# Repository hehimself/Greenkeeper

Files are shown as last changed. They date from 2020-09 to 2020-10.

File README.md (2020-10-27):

# Greenkeeper





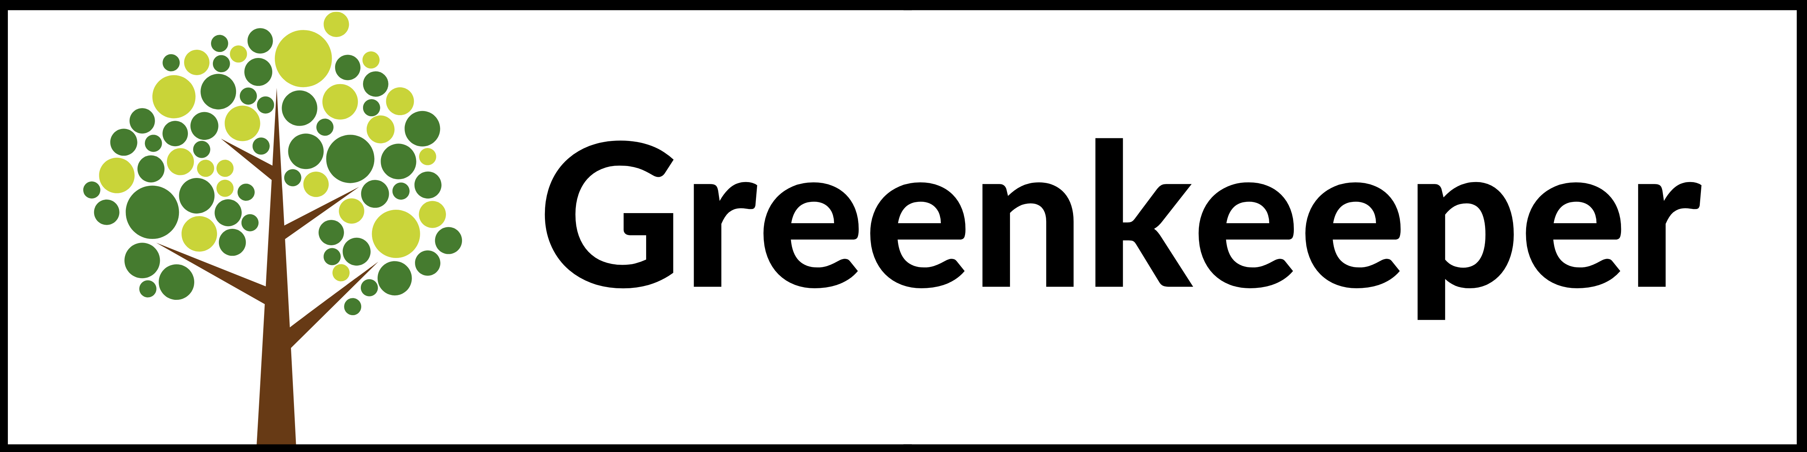
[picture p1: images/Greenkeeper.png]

Der Arduino Greenkeeper ist ein vollautomatisiertes Bewässerungssystem für eine Zimmerpflanze.
Zu Beginn habe ich eine Platine mithilfe von KiCAD erstellt. Auf der Platine können alle wichtigen Teile direkt verlötet werden. Die SMD LEDs helfen, den Status des Bewässerungssystems zu erkennen. Auf dem OLED Display werden die Messwerte wie Bodenfeuchtigkeit, Temperatur, Lichtstärke usw dargestellt. Zudem gibt es ein Menü, welches sich durch die Buttons steuern lässt.
(Schaltplan unter: schema.pdf)

## Funktionsweise
### 1. Die Bewässerung
Die Bewässerungsanlage ist recht simple aufgebaut. Es wird mithilfe des Sensor die Bodenfeuchtigkeit gemessen. Wenn der Messwert einen gewissen Wert überschreitet wird die Pumpe mithilfe des Relais für eine Sekunde aktiviert. Alle 10 Sekunden wird die Bodenfeuchtigkeit gemessen. Somit wird sichergestellt, das die Pflanze immer genügend Wasser zur Verfügung hat.

```C++
void Bewaesserungssystem() {
  //Als erstes wird eine Bodenmessung durchgeführt
  Bodenmessung();
//Falls der Boden zu trocken ist wird die Pumpe eingeschalten
  if (Bodensensor_Messwert >= 450) {        //Dieser Wert ist natürlich abhängig von Pflanze und Sensor
    if (Pumpe_Auto == 1) {
      LED_D12_Status = 1;
      LED_Steuerung();
      digitalWrite(Pumpe, LOW);
      Pumpe_counter ++;
      delay(1000);
      digitalWrite(Pumpe, HIGH);
      LED_D12_Status = 0;
    } else {
      LED_D11_Status = 1;
    }  
  } else {
    LED_D11_Status = 1;
  }
}
```

### 2. Die Status LEDs
Die Status LEDs die am meisten angeschalten sind werden, je nach Helligkeit automatisch gedimmt. Diese sind am Arduino an den PWM (Pulse Width Modulation) fähigen Pins angeschlossen.

POWER Diese LED zeigt, ob die Platine mit Strom versorgt wird
STATUS (gelb) Diese blinkt wenn etwas mit der Bewässerung nicht stimmt
STATUS (grün) Diese LED leuchtet wenn die Pflanze genügend Wasser hat
PUMPE Diese LED leuchtet wenn die Pumpe läuft
W-Tank Diese LED leuchtet, wenn der Wassertank leer ist.
FEHLER (noch ohne funktion)

### 3. Die Tasten
Taster von links nach rechts:

Menü Button
"Down" Button
"UP" Button
"ENTER" Button

### 4. Das Display
Auf dem Dashboard wird der Messwert der Bodenmessung, die Temperatur und der Messwert des Lichtsensor dargestellt. Wenn man zum Menü kommen will muss man nur den "Menü" Button betätigen (1. Button von links). Um wieder zurück zum Dashboard zu kommen wählt man im Menü den Punk "Dashboard" aus.

Das Menü hat folgende weitere Funktionen:

PUMP Automatik Hierbei lässt sich die Bewässerung ausschalten um sicher zu gehen das die Pumpe nicht läuft, obwohl der Sensor beispielsweise aus der Pflanze genommen wurde.
Nachtmodus Der Nachtmodus lässt sich über das Menü aktivieren/deaktivieren. Während der Nachtmodus aktiviert ist gehen alle Status LEDs aus.
Display Mit diesem Menü Punkt lässt sich das Display ausschalten, sodass alles Dunkel ist. Wenn man das Display wieder anschalten möchte muss man einfach den "Menü" Button (Button_S1) drücken.
Transistor Mithilfe dieser Funktion, lassen sich die Grünen LEDs unten manuell anschalten. Diese sind jedoch zurzeit nur für ein schönes aussehen und noch komplett ohne eine sinnvolle Funktion

## Die Platine
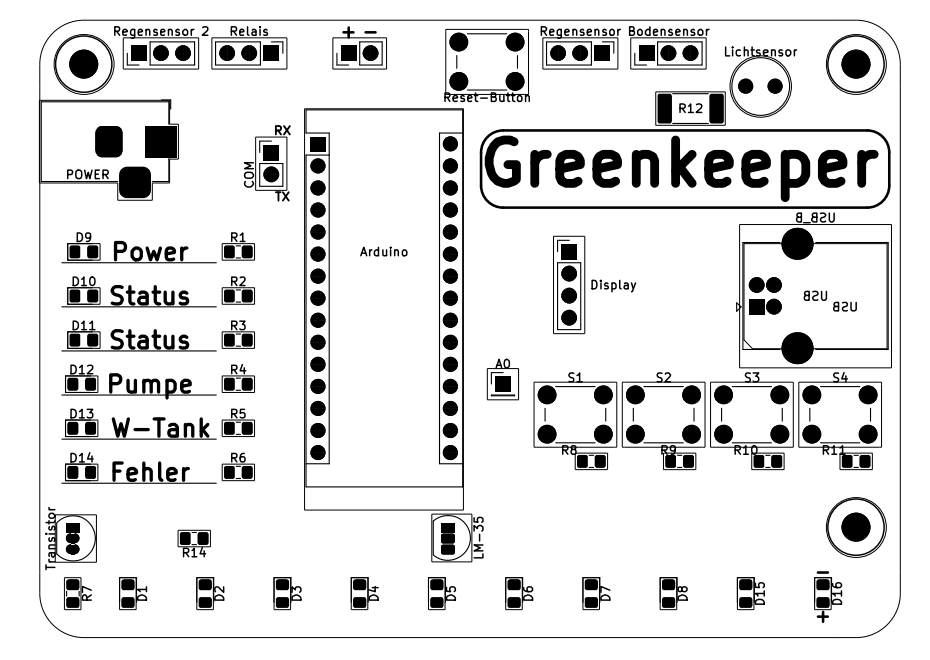
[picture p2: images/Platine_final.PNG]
Platine


## Übersicht zu Widerständen und Leds
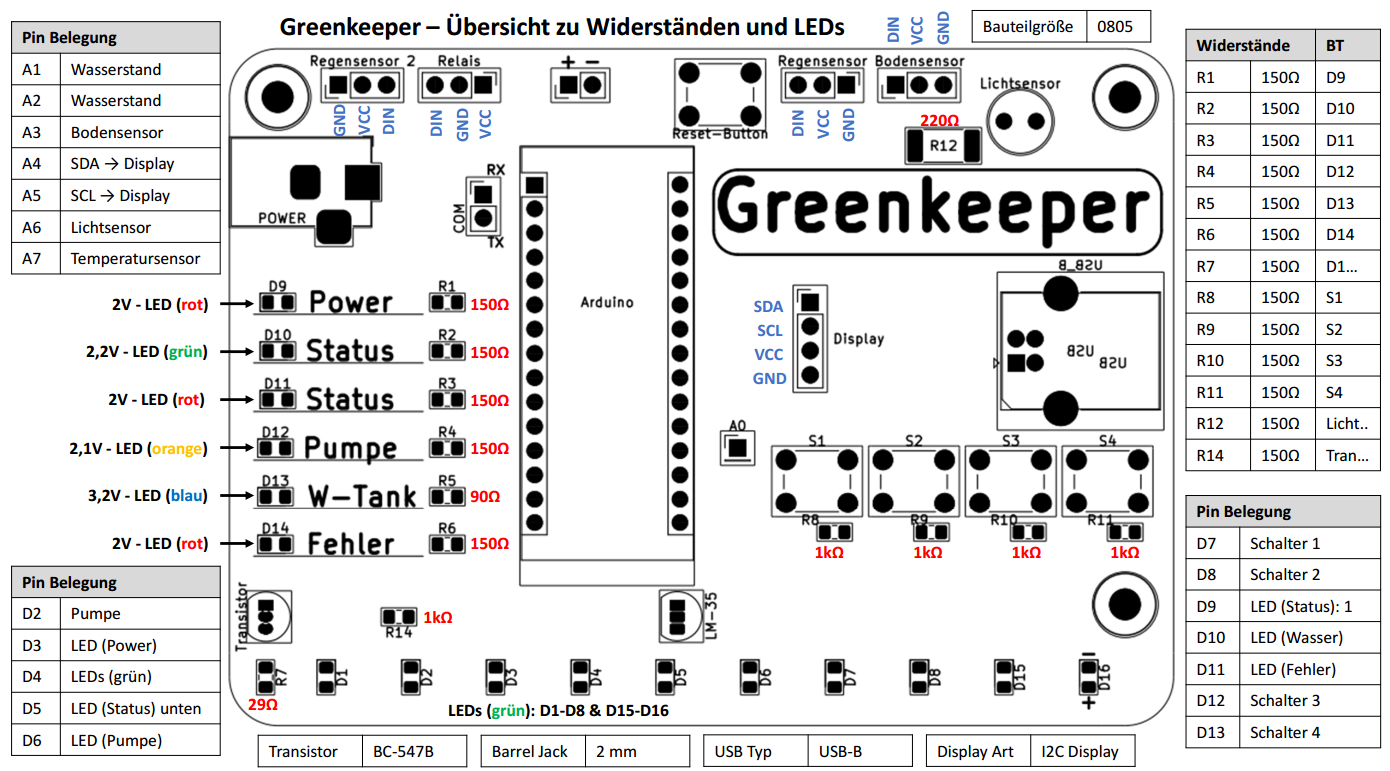
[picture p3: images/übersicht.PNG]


# Bauanleitung
Die Gesamte Anleitung gibts hier: [hackster.io](https://www.hackster.io/ms2002maerz14/arduino-greenkeeper-687363)
WARNUNG: Man sollte bereits Erfahrung im löten von SMD Komponenten der Größe 0805 besitzen, da sonst die Komponenten oder die Platine beschädigt werden können.

### Platine löten

Ich rate aus eigener Erfahrung mehrere Platinen und mehr Komponenten als angegeben sich zu kaufen, da es sehr schnell gehen kann eine SMD Komponente zu zerstören. Am Besten nimmt man sich die Übersicht zu Widerständen uns LEDs zur Hilfe während des löten, um zu wissen, welches Bauteil, wo gelötet werden muss.

### Platine testen

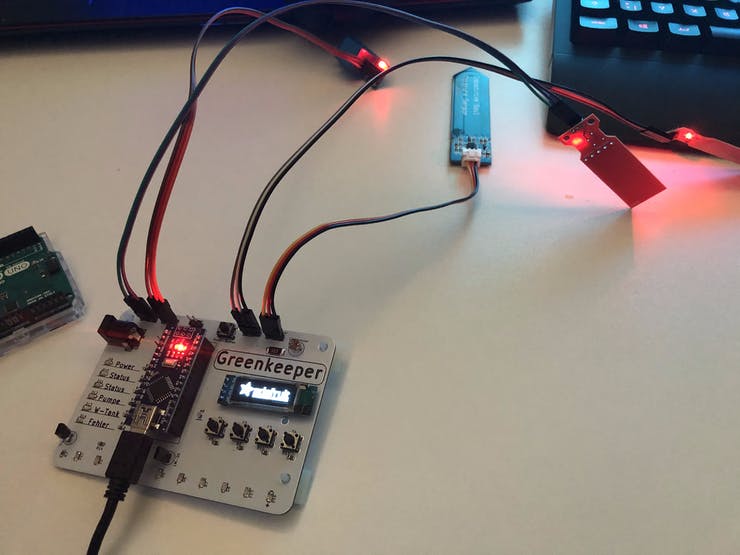
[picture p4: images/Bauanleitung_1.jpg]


Zum testen aller Funktionen und zum Einstellen der Parameter der Sensoren habe ich die Platine per USB mit dem Computer verbunden und nacheinander alle Sensoren, Schalter und Display getestet.

### Inbetriebnahme

Am Besten befestigt man den Schlauch mit ein bisschen Tesafilm an dem Topf, damit dieser während der Bewässerung nicht verrutscht. Zudem ist es nun Zeit den Sensor für die Bodenfeuchtigkeit in die Erde zu stecken.

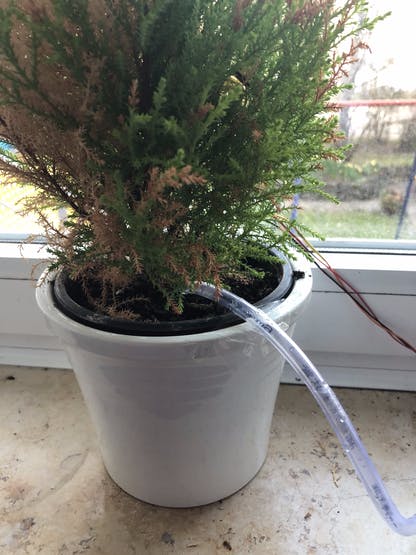
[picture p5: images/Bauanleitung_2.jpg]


Nun ist es Zeit sich um den Wassertank zu kümmer. Hierbei empfehle ich die Pumpe am Boden des Behälters oder des Tanks festzukleben. Das Relais habe ich in meinem Fall einfach an die Seite des Wasserbehälter geklebt (siehe Abbildung unten)

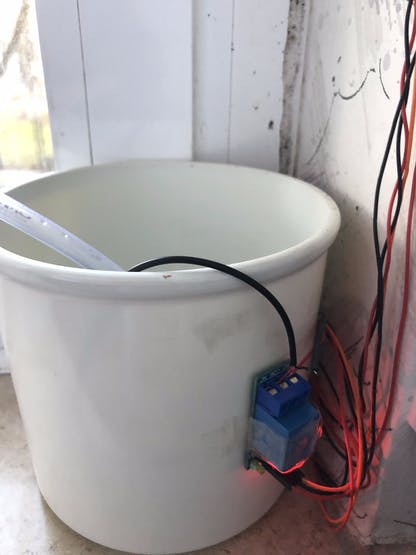
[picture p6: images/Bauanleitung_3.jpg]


Die Platine habe ich mithilfe von Platinen Abstandshalter an der Wand befestigt und im Anschluss alle Anschlüsse verkabelt. Die Stromversorgung erfolgt über ein Netzteil (9V). Eine Versorgung über USB ist zwar möglich jedoch wenn alle LEDs angeschalten sind und die Pumpe läuft, ist man an der Spitze der Leistung des Arduino. Das Bewässerungssystem ist nun einsatzbereit. Eventuell muss man im Code den Wert, ab wann die Pumpe pumpt noch für seine Pflanze anpassen.

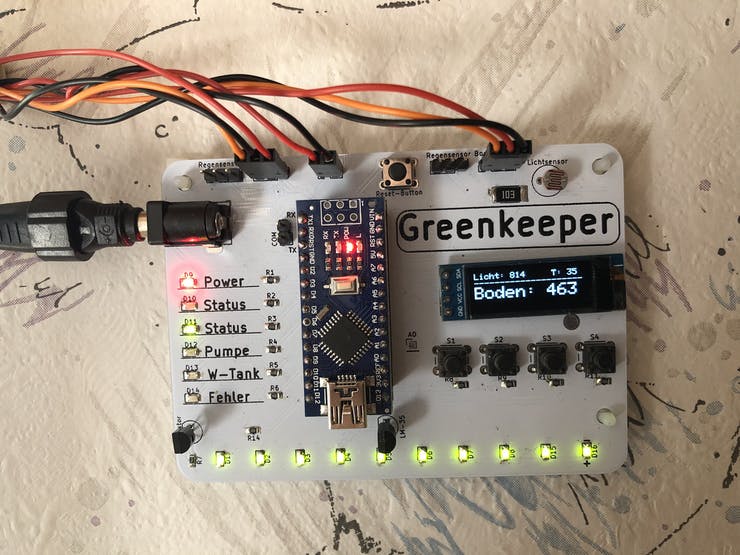
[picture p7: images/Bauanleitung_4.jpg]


Fertig...

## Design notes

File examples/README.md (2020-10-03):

## Code Beispiele
Diese Code Beispiele dienen zum testen der einzelnen Komponenten

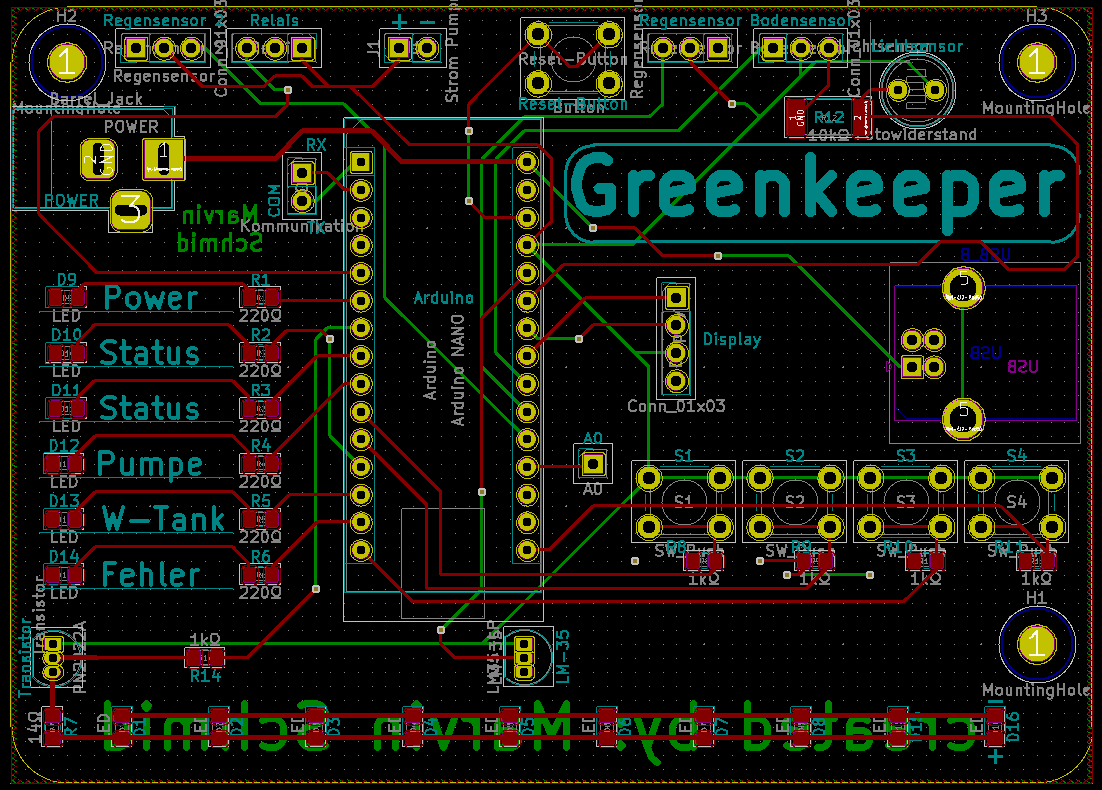
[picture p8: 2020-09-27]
images/Platine final.PNG

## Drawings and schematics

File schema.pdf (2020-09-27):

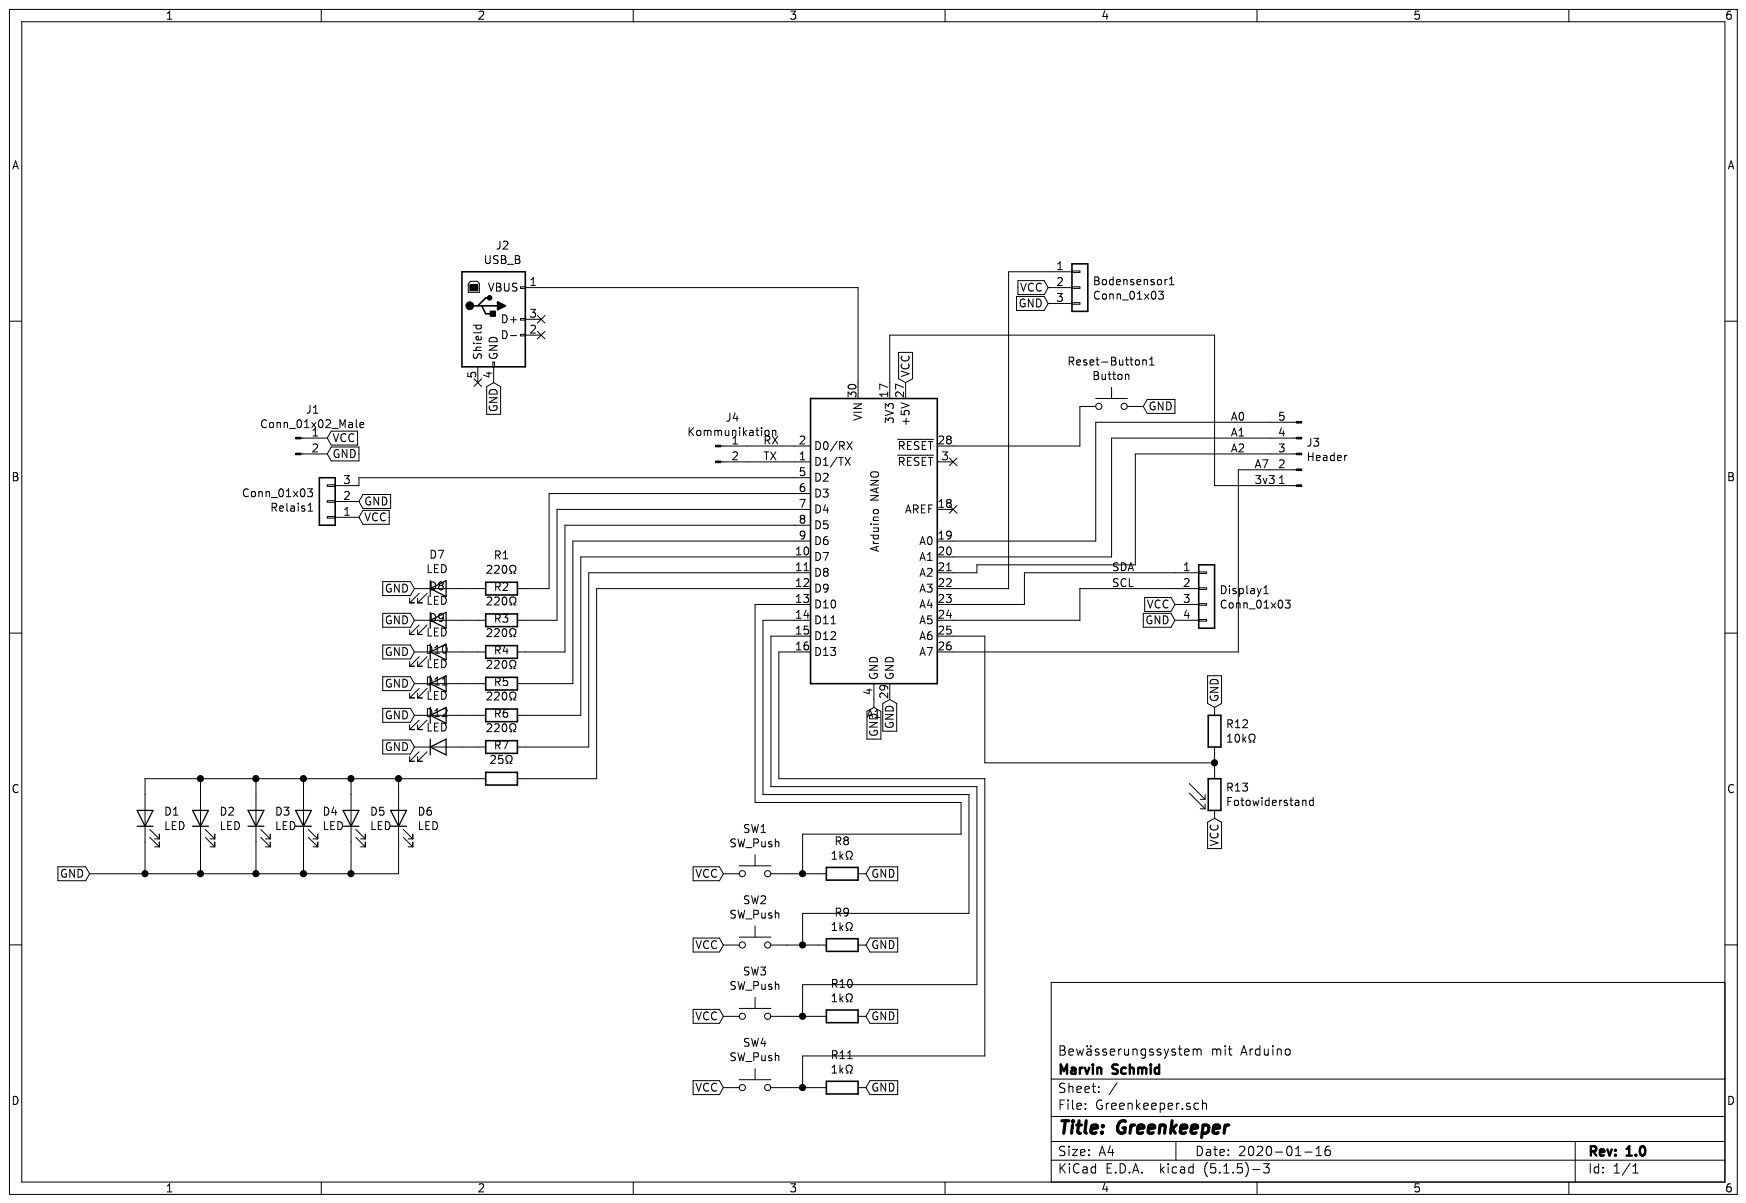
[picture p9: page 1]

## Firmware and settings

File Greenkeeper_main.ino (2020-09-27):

/* ---------------------------------------------------------*
 *                                                          *
 *    Projekt: Arduino Greenkeeper - Bewässerungssystem     *
 *                                                          *
 *    Name: Marvin Schmid                                   *
 *                                                          *
 *    Version: 1.5                                          *
 *                                                          *
 * ---------------------------------------------------------*
*/
//Bibliotheken
#include <SPI.h>
#include <Wire.h>
//Bibliotheken für den betrieb des Displays
#include <Adafruit_GFX.h>
#include <Adafruit_SSD1306.h>
 
#define OLED_RESET 4
Adafruit_SSD1306 display(OLED_RESET);

//Arduino LEDs
const int LED_D9 = 3;
const int LED_D10 = 9;
const int LED_D11 = 5;
const int LED_D12 = 6;
const int LED_D13 = 10;
const int LED_D14 = 11;
const int LED_Transistor = 4;
int LED_D9_Status = 0;
int LED_D10_Status = 0;
int LED_D11_Status = 0;
int LED_D12_Status = 0;
int LED_D13_Status = 0;
int LED_D14_Status = 0;
int LED_D9_Helligkeit = 0;
int LED_D11_Helligkeit = 0;
int LED_D12_Helligkeit = 0;
int LED_D13_Helligkeit = 0;
int LED_D14_Helligkeit = 0;

//Nachtmodus
int led_nachtmodus = 0;

//Arduino Schalter
const int Button_1 = 7;
const int Button_2 = 8;
const int Button_3 = 12;
const int Button_4 = 13;

//Pumpe und Pumpautomatik
const int Pumpe = 2;
int Pumpe_Auto = 0;
int Pumpe_counter = 0;

//Arduino Sensoren
const int Bodensensor = A3;
const int Wasserstand_1 = A1;
const int Wasserstand_2 = A2;
const int Lichtsensor = A6;
const int Temperatursensor = A7;
int Bodensensor_Messwert = 0;
int Wasserstand_1_Messwert = 0;
int Wasserstand_2_Messwert = 0;
int Lichtsensor_Messwert = 0;
int Temperatursensor_Messwert = 0;
int Temperatur = 0;

//Wichtig statt Delay
unsigned long LED_D10_timeMillis = 0;
unsigned long LED_D14_timeMillis = 0;
unsigned long LED_Transistor_timeMillis = 0;
unsigned long previousMillis1= 0;
unsigned long previousMillis2 = 0;
unsigned long previousMillis3 = 0;
unsigned long previousMillis4 = 0;
unsigned long previousMillis5_unbenutzt = 0;
unsigned long previousMillis6_unbenutzt = 0;
unsigned long previousMillis7_unbenutzt = 0;
unsigned long previousMillis8_unbenutzt = 0;
const long interval1 = 10000;   //10 Sekunden
const long interval2 = 1000;    //1 Sekunde
const long interval3 = 25050;   //ca. 25 Sekunden
const long interval4 = 600000;  //10 Minuten
const long interval5_unbenutzt = 1000;
const long interval6_unbenutzt = 1000;
const long interval7_unbenutzt = 1000;
const long interval8_unbenutzt = 1000;

//Display Menu
int menu = 1;

void setup() {
  digitalWrite(Pumpe, HIGH);
  //Kommunikation
  Serial.begin(9600);

  //Sensoren und Aktoren
  pinMode(Pumpe, OUTPUT);
  pinMode(Button_1, INPUT);
  pinMode(Button_2, INPUT);
  pinMode(Button_3, INPUT);
  pinMode(Button_4, INPUT);
  pinMode(LED_D9, OUTPUT);
  pinMode(LED_D10, OUTPUT);
  pinMode(LED_D11, OUTPUT);
  pinMode(LED_D12, OUTPUT);
  pinMode(LED_D13, OUTPUT);
  pinMode(LED_D14, OUTPUT);
  pinMode(LED_Transistor, OUTPUT);
  
  //Display Konfigurationen
  display.begin(SSD1306_SWITCHCAPVCC, 0x3C);
  display.display();

  //Startsequenz
  Startsequenz();
  
  //Iniziere das Menu
  updateMenu();
  
  //Zeit für blinkende LED
  LED_D10_timeMillis = millis();
  
  //Dafault für Automatik
  Pumpe_Auto = 1;
  led_nachtmodus = 0;
  digitalWrite(LED_Transistor, LOW);
  digitalWrite(Pumpe, HIGH);
}
void loop() {
  SERIAL_COMMUNICATION();
  LED_Steuerung();
  BUTTON_Steuerung();
  updateMenu();
  //Tropfensensor jede Stunde lesen
  unsigned long currentMillis4 = millis();
  if (currentMillis4 - previousMillis4 >= interval4) {
    previousMillis4 = currentMillis4;
    //Tropfensensor();
  }
  //Lichtmessung alle 15 Minuten aufrufen
  unsigned long currentMillis3 = millis();
  if (currentMillis3 - previousMillis3 >= interval3) {
    previousMillis3 = currentMillis3;
    Temperaturmessung();
  }
  //Lichtmessung alle 1 Sekunde aufrufen
  unsigned long currentMillis2 = millis();
  if (currentMillis2 - previousMillis2 >= interval2) {
    previousMillis2 = currentMillis2;
    Lichtmessung();
  }
  //Bewaesserungssystem alle 15 Minuten aufrufen
  unsigned long currentMillis1 = millis();
  if (currentMillis1 - previousMillis1 >= interval1) {
    previousMillis1= currentMillis1;
    Bewaesserungssystem();
  }
}
void Lichtmessung() {
  //Lichtmessung mit Hilfe der Photozelle wird durchgeführt
  Lichtsensor_Messwert = analogRead(Lichtsensor);
}
void Temperaturmessung() {
  //Temperaturmessung mit LM35
  Temperatursensor_Messwert = analogRead(Temperatursensor); 
  Temperatur = map(Temperatursensor_Messwert, 0, 307, 0, 150); 
}
void Bewaesserungssystem() {
  //Als erstes wird eine Bodenmessung durchgeführt
  Bodenmessung();

  //Falls der Boden zu trocken ist wird die Pumpe eingeschalten
  if (Bodensensor_Messwert >= 450) {
    if (Pumpe_Auto == 1) {
      LED_D12_Status = 1;
      LED_Steuerung();
      digitalWrite(Pumpe, LOW);
      Pumpe_counter ++;
      delay(1000);
      digitalWrite(Pumpe, HIGH);
      LED_D12_Status = 0;
    } else {
      LED_D11_Status = 1;
    }  
  } else {
    LED_D11_Status = 1;
  }
}
void Bodenmessung() {
  Bodensensor_Messwert = analogRead(Bodensensor); 
  Serial.println(Bodensensor_Messwert);
}
void Tropfensensor() {
  Wasserstand_1_Messwert = analogRead(Wasserstand_1);
  Wasserstand_2_Messwert = analogRead(Wasserstand_2);
}
void Startsequenz() {
  //Dieser Code wird nach dem Einschalten ausgeführt
  //LED Startsequenz
  digitalWrite(LED_Transistor, HIGH);
  delay(500);
  digitalWrite(LED_Transistor, LOW);
  for (int helligkeit =1; helligkeit <= 255; helligkeit = helligkeit +1){
    analogWrite(LED_D9, helligkeit);
    delay(1);
  }
  for (int helligkeit =255; helligkeit >= 0; helligkeit = helligkeit -1){
    analogWrite(LED_D9, helligkeit);
    delay(1);
  }
  for (int helligkeit =1; helligkeit <= 255; helligkeit = helligkeit +1){
    analogWrite(LED_D10, helligkeit);
    delay(1);
  }
  for (int helligkeit =255; helligkeit >= 0; helligkeit = helligkeit -1){
    analogWrite(LED_D10, helligkeit);
    delay(1);
  }
  for (int helligkeit =1; helligkeit <= 255; helligkeit = helligkeit +1){
    analogWrite(LED_D11, helligkeit);
    delay(1);
  }
  for (int helligkeit =255; helligkeit >= 0; helligkeit = helligkeit -1){
    analogWrite(LED_D11, helligkeit);
    delay(1);
  }
  for (int helligkeit =1; helligkeit <= 255; helligkeit = helligkeit +1){
    analogWrite(LED_D12, helligkeit);
    delay(1);
  }
  for (int helligkeit =255; helligkeit >= 0; helligkeit = helligkeit -1){
    analogWrite(LED_D12, helligkeit);
    delay(1);
  }
  for (int helligkeit =1; helligkeit <= 255; helligkeit = helligkeit +1){
    analogWrite(LED_D13, helligkeit);
    delay(1);
  }
  for (int helligkeit =255; helligkeit >= 0; helligkeit = helligkeit -1){
    analogWrite(LED_D13, helligkeit);
    delay(1);
  }
  for (int helligkeit =1; helligkeit <= 255; helligkeit = helligkeit +1){
    analogWrite(LED_D14, helligkeit);
    delay(1);
  }
  for (int helligkeit =255; helligkeit >= 0; helligkeit = helligkeit -1){
    analogWrite(LED_D14, helligkeit);
    delay(1);
  }
  for (int helligkeit =1; helligkeit <= 255; helligkeit = helligkeit +1){
    analogWrite(LED_D14, helligkeit);
    analogWrite(LED_D13, helligkeit);
    analogWrite(LED_D12, helligkeit);
    analogWrite(LED_D11, helligkeit);
    analogWrite(LED_D10, helligkeit);
    analogWrite(LED_D9, helligkeit);
    delay(3);
  }
  for (int helligkeit =255; helligkeit >= 0; helligkeit = helligkeit -1){
    analogWrite(LED_D14, helligkeit);
    analogWrite(LED_D13, helligkeit);
    analogWrite(LED_D12, helligkeit);
    analogWrite(LED_D11, helligkeit);
    analogWrite(LED_D10, helligkeit);
    analogWrite(LED_D9, helligkeit);
    delay(3);
  }
  for (int i = 1; i <= 2; i = i+1) {
    digitalWrite(LED_D9, HIGH);
    delay(50);
    digitalWrite(LED_D10, HIGH);
    delay(50);
    digitalWrite(LED_D11, HIGH);
    delay(50);
    digitalWrite(LED_D12, HIGH);
    delay(50);
    digitalWrite(LED_D13, HIGH);
    delay(50);
    digitalWrite(LED_D14, HIGH);
    delay(200);
    digitalWrite(LED_D9, LOW);
    delay(50);
    digitalWrite(LED_D10, LOW);
    delay(50);
    digitalWrite(LED_D11, LOW);
    delay(50);
    digitalWrite(LED_D12, LOW);
    delay(50);
    digitalWrite(LED_D13, LOW);
    delay(50);
    digitalWrite(LED_D14, LOW);
    delay(200);
    digitalWrite(LED_D14, HIGH);
    delay(50);
    digitalWrite(LED_D13, HIGH);
    delay(50);
    digitalWrite(LED_D12, HIGH);
    delay(50);
    digitalWrite(LED_D11, HIGH);
    delay(50);
    digitalWrite(LED_D10, HIGH);
    delay(50);
    digitalWrite(LED_D9, HIGH);
    delay(200);
    digitalWrite(LED_D14, LOW);
    delay(50);
    digitalWrite(LED_D13, LOW);
    delay(50);
    digitalWrite(LED_D12, LOW);
    delay(50);
    digitalWrite(LED_D11, LOW);
    delay(50);
    digitalWrite(LED_D10, LOW);
    delay(50);
    digitalWrite(LED_D9, LOW);
    delay(200);
  }
  for (int i = 0; i <= 2; i = i+1) {
    delay(100);
    for (int helligkeit =1; helligkeit <= 255; helligkeit = helligkeit +1){
      analogWrite(LED_D14, helligkeit);
      analogWrite(LED_D13, helligkeit);
      analogWrite(LED_D12, helligkeit);
      analogWrite(LED_D11, helligkeit);
      analogWrite(LED_D10, helligkeit);
      analogWrite(LED_D9, helligkeit);
      delay(1);
    }
    for (int helligkeit =255; helligkeit >= 0; helligkeit = helligkeit -1){
      analogWrite(LED_D14, helligkeit);
      analogWrite(LED_D13, helligkeit);
      analogWrite(LED_D12, helligkeit);
      analogWrite(LED_D11, helligkeit);
      analogWrite(LED_D10, helligkeit);
      analogWrite(LED_D9, helligkeit);
      delay(1);
    }
  }
  menu = 10;
  //POWER LED an
  LED_D9_Status = 1;
}
void BUTTON_Steuerung() {
  if (digitalRead(Button_1) == HIGH){
    menu = 1;
    updateMenu();
    delay(500);
  }
  if (digitalRead(Button_2) == HIGH){
    delay(500);
  }
  if (digitalRead(Button_3) == HIGH){
    menu++;
    updateMenu();
    delay(500);
  }
  if (digitalRead(Button_4) == HIGH){
    excecuteAction();
    updateMenu();
    delay(500);
  }
}
void updateMenu() {
  switch (menu)
  {
  case 0:
    menu = 1;
    break;
  case 1:
    display.clearDisplay();
    display.setTextSize(1);
    display.setTextColor(WHITE);
    display.setCursor(0,0);
    display.println("> Pumpe");
    display.setCursor(0,8);
    display.println("  LEDs");
    display.setCursor(0,16);
    display.println("  Transistor");
    display.setCursor(0,24);
    display.println("  Wasserstand");
    display.display();
    break;
  case 2:
    display.clearDisplay();
    display.setTextSize(1);
    display.setTextColor(WHITE);
    display.setCursor(0,0);
    display.println("  Pumpe");
    display.setCursor(0,8);
    display.println("> LEDs");
    display.setCursor(0,16);
    display.println("  Transistor");
    display.setCursor(0,24);
    display.println("  Wasserstand");
    display.display();
    break;
  case 3:
    display.clearDisplay();
    display.setTextSize(1);
    display.setTextColor(WHITE);
    display.setCursor(0,0);
    display.println("  Pumpe");
    display.setCursor(0,8);
    display.println("  LEDs");
    display.setCursor(0,16);
    display.println("> Transistor");
    display.setCursor(0,24);
    display.println("  Wasserstand");
    display.display();
    break;
  case 4:
    display.clearDisplay();
    display.setTextSize(1);
    display.setTextColor(WHITE);
    display.setCursor(0,0);
    display.println("  Pumpe");
    display.setCursor(0,8);
    display.println("  LEDs");
    display.setCursor(0,16);
    display.println("  Transistor");
    display.setCursor(0,24);
    display.println("> Wasserstand");
    display.display();
    break;
  case 5:
    display.clearDisplay();
    display.setTextSize(1);
    display.setTextColor(WHITE);
    display.setCursor(0,0);
    display.println(">  Display");
    display.setCursor(0,8);
    display.println("   Dashboard");
    display.setCursor(0,16);
    display.println("----------------");
    display.display();
    break;
  case 6:
    display.clearDisplay();
    display.setTextSize(1);
    display.setTextColor(WHITE);
    display.setCursor(0,0);
    display.println("   Display");
    display.setCursor(0,8);
    display.println(">  Dashboard");
    display.setCursor(0,16);
    display.println("----------------");
    display.display();
    break;
  case 7:
    menu = 1;
    break;
  case 8:
    display.clearDisplay();
    display.display();
    break;
  case 10:
    display.clearDisplay();
    display.setTextSize(1);
    display.setTextColor(WHITE);
    display.setCursor(0,0);
    display.print("Licht: ");
    display.print(Lichtsensor_Messwert);
    display.setCursor(90,0);
    display.print("T: ");
    display.println(Temperatur);
    display.setCursor(0,8);
    display.println("---------------------");
    display.setTextSize(2);
    display.setCursor(0,16);
    display.print("Boden: ");
    display.println(Bodensensor_Messwert);
    display.display();
    break;
  }
}
void excecuteAction() {
  switch (menu) {
    case 1:
      action1();
      break;
    case 2:
      action2();
      break;
    case 3:
      action3();
      break;
    case 4:
      action4();
      break;
    case 5:
      action5();
      break;
    case 6:
      action6();
      break;
  }
}
void action1() {
  if (Pumpe_Auto == 1) {
    display.clearDisplay();
    display.setTextSize(1);
    display.setTextColor(WHITE);
    display.setCursor(0,0);
    display.println("Pumpautomatik wird");
    display.setCursor(0,8);
    display.println("ausgeschalten");
    display.display();
    Pumpe_Auto = 0;
    updateMenu();
  } else {
    if (Pumpe_Auto == 0) {
      display.clearDisplay();
      display.setTextSize(1);
      display.setTextColor(WHITE);
      display.setCursor(0,0);
      display.println("Pumpautomatik wird");
      display.setCursor(0,8);
      display.println("angeschalten");
      display.display();
      Pumpe_Auto = 1;
      updateMenu();
    }
  }
  delay(3000);
}
void action2() {
  if (led_nachtmodus == 0) {
    display.clearDisplay();
    display.setTextSize(1);
    display.setTextColor(WHITE);
    display.setCursor(0,0);
    display.println("Nachtmodus wird");
    display.setCursor(0,8);
    display.println("angeschalten");
    display.display();
    led_nachtmodus = 1;
    menu = 10;
    updateMenu();
  } else {
    if (led_nachtmodus == 1) {
      display.clearDisplay();
      display.setTextSize(1);
      display.setTextColor(WHITE);
      display.setCursor(0,0);
      display.println("Nachtmodus wird");
      display.setCursor(0,8);
      display.println("ausgeschalten");
      display.display();
      led_nachtmodus = 0;
      menu = 10;
      updateMenu();
    }
  }
  delay(3000);
}
void action3() {
  digitalWrite(LED_Transistor, !digitalRead(LED_Transistor));
  display.clearDisplay();
  display.setTextSize(1);
  display.setTextColor(WHITE);
  display.setCursor(0,0);
  display.println("Transistor wird");
  display.setCursor(0,8);
  display.println("an/ausgeschalten");
  display.display();
  delay(3000);
  menu = 10;
  updateMenu();
}
void action4() {
  display.clearDisplay();
  display.setTextSize(1);
  display.setTextColor(WHITE);
  display.setCursor(0,0);
  display.print("Wasserstand 1:");
  display.print(Wasserstand_1_Messwert);
  display.setCursor(0,8);
  display.print("Wasserstand 2:");
  display.print(Wasserstand_2_Messwert);
  display.display();
  delay(3000);
  menu = 10;
  updateMenu();
}
void action5() {
  display.clearDisplay();
  display.setTextSize(1);
  display.setTextColor(WHITE);
  display.setCursor(0,0);
  display.print("Display aus");
  display.display();
  delay(2000);
  display.clearDisplay();
  display.display();
  menu = 8;
  updateMenu();
}
void action6() {
  display.clearDisplay();
  display.setTextSize(2);
  display.setTextColor(WHITE);
  display.setCursor(0,0);
  display.print("_________");
  display.setCursor(0,16);
  display.print("Dashboard");
  display.display();
  delay(1000);
  menu = 10;
  updateMenu();
}
void LED_Steuerung() {
  //Check ob der Nachtmodus an oder ausgeschalten ist
  if (led_nachtmodus == 0) {
    //Check LED D9
    if (LED_D9_Status == 1) {
      LED_D9_Helligkeit = map(Lichtsensor_Messwert, 0, 1023, 1, 5);
      LED_D9_Helligkeit = map(LED_D9_Helligkeit, 1, 5, 5, 220);
      analogWrite(LED_D9, LED_D9_Helligkeit);
    } else {
      digitalWrite(LED_D9, LOW);
    }
    //Check LED_D10
    if (LED_D10_Status == 1) {
      if ((millis() - LED_D10_timeMillis) >= 500) {
      digitalWrite(LED_D10, !digitalRead(LED_D10));
      LED_D10_timeMillis = millis();
    }
    } else {
      digitalWrite(LED_D10, LOW);
    }
    //Check LED_D11
    if (LED_D11_Status == 1) {
      LED_D11_Helligkeit = Lichtsensor_Messwert;
      if (LED_D11_Helligkeit <= 200)  {
        analogWrite(LED_D11, 100);
      } 
      else {
        digitalWrite(LED_D11, HIGH);
      }
    } else {
      digitalWrite(LED_D11, LOW);
    }
    //Check LED_D12
    if (LED_D12_Status == 1) {
      digitalWrite(LED_D12, HIGH);
    } else {
      digitalWrite(LED_D12, LOW);
    }
    //Check LED_D13
    if (LED_D13_Status == 1) {
      LED_D13_Helligkeit = map(Lichtsensor_Messwert, 0, 1023, 1, 5);
      LED_D13_Helligkeit = map(LED_D13_Helligkeit, 1, 5, 5, 255);
      analogWrite(LED_D13, LED_D13_Helligkeit);
    } else {
      digitalWrite(LED_D13, LOW);
    }
    //Check LED_D14
    if (LED_D14_Status == 1) {
      if ((millis() - LED_D14_timeMillis) >= 500) {
      digitalWrite(LED_D14, !digitalRead(LED_D14));
      LED_D14_timeMillis = millis();
    }
    } else {
      digitalWrite(LED_D14, LOW);
    }
  } else {
    digitalWrite(LED_D9, LOW);
    digitalWrite(LED_D10, LOW);
    digitalWrite(LED_D11, LOW);
    digitalWrite(LED_D12, LOW);
    digitalWrite(LED_D13, LOW);
    digitalWrite(LED_D14, LOW);
    digitalWrite(LED_Transistor, LOW);
  }
}
void SERIAL_COMMUNICATION() {
  //Serielle Kommunation mit dem Raspberry Pi über eine USB Verbindung
  //so können Befehle direkt an den Greenkeeper gesendet werden
  if (Serial.available() ){
    byte empfangen = Serial.read();
    switch (empfangen)  {
      case 48:      //ASCII = 0
        action1();  //Pumpautomatik wird aus- oder eingeschalten
        break;
      case 49:      //ASCII = 1
        action2();  //Nachtmodus wird aus- oder eingeschalten
        break;
      case 50:      //ASCII = 2
        action3();  //Transistor wird aus- oder eingeschalten
        break;
      case 51:      //ASCII = 3
        action5();  //Display wird ausgeschalten
        break;
      case 52:      //ASCII = 4
        LED_D10_Status = 1;
        LED_Steuerung();
        break;
      case 53:      //ASCII = 5
        LED_D10_Status = 0;
        LED_Steuerung();
        break;
      case 54:      //ASCII = 6
        LED_D14_Status = 1;
        LED_Steuerung();
        break;
      case 55:      //ASCII = 7
        LED_D14_Status = 0;
        LED_Steuerung();
        break;
      case 56:      //ASCII = 8
        delay(1);   //NOCH OHNE FUNKTION
        break;
      case 57:      //ASCII = 9
        delay(1);   //NOCH OHNE FUNKTION
        break;
      }
    }
}

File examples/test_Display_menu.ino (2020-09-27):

/*-----------------------------------------------
 * 
 *    Projekt: Arduino Greenkeeper - Bewässerungssystem
 * 
 *    Name: Marvin Schmid
 * 
 *    Version: 0.2
 * 
 * -----------------------------------------------
*/
//Bibliotheken
#include <SPI.h>
#include <Wire.h>
//Bibliotheken für den betrieb des Displays
#include <Adafruit_GFX.h>
#include <Adafruit_SSD1306.h>
 
#define OLED_RESET 4
Adafruit_SSD1306 display(OLED_RESET);

const unsigned char Greenkeeper_IMAGE [] = {
0x80, 0x00, 0x20, 0x00, 
0x00, 0x00, 0x00, 0x00, 0x00, 0x00, 0x00, 0x00, 0x00, 0x00, 0x00, 0x00, 0x00, 0x00, 0x00, 0x00,
0x00, 0x00, 0x00, 0x00, 0x00, 0x00, 0x00, 0x00, 0x00, 0x00, 0x00, 0x00, 0x00, 0x00, 0x00, 0x00,
0x00, 0x00, 0x00, 0x00, 0x00, 0x00, 0x00, 0x00, 0x00, 0x00, 0x00, 0x00, 0x00, 0x00, 0x00, 0x00,
0x00, 0x00, 0x00, 0x00, 0x00, 0x00, 0x00, 0x00, 0x00, 0x00, 0x00, 0x00, 0x00, 0x00, 0x00, 0x00,
0x00, 0x00, 0x00, 0x00, 0x00, 0x00, 0x00, 0x00, 0x00, 0x00, 0x00, 0x00, 0x00, 0x00, 0x00, 0x00,
0x00, 0x00, 0x00, 0x00, 0x00, 0x00, 0x00, 0x00, 0x00, 0x00, 0x00, 0x00, 0x00, 0x00, 0x00, 0x00,
0x00, 0x00, 0x00, 0x00, 0x00, 0x00, 0x00, 0x00, 0x00, 0x00, 0x00, 0x00, 0x00, 0x00, 0x00, 0x00,
0x00, 0x00, 0x00, 0x00, 0x00, 0x00, 0x00, 0x00, 0x00, 0x00, 0x00, 0x00, 0x00, 0x00, 0x00, 0x00,
0x00, 0x00, 0x00, 0x00, 0x00, 0x00, 0x00, 0x00, 0x00, 0x00, 0x00, 0x00, 0x00, 0x00, 0x00, 0x00,
0x00, 0x00, 0x00, 0x00, 0x00, 0x00, 0x00, 0x00, 0x00, 0x00, 0x00, 0x00, 0x00, 0x00, 0x00, 0x00,
0x00, 0x00, 0x00, 0x00, 0x00, 0x00, 0x00, 0x00, 0x00, 0x02, 0x00, 0x00, 0x00, 0x00, 0x00, 0x00,
0x00, 0x00, 0x00, 0x00, 0x00, 0x84, 0x00, 0x00, 0x00, 0x02, 0x00, 0x00, 0x00, 0x00, 0x00, 0x00,
0x00, 0x00, 0x00, 0x00, 0x01, 0x00, 0x00, 0x00, 0x00, 0x02, 0x00, 0x00, 0x00, 0x00, 0x00, 0x00,
0x00, 0x00, 0x00, 0x00, 0x02, 0x00, 0x00, 0x00, 0x00, 0x02, 0x00, 0x00, 0x00, 0x00, 0x00, 0x00,
0x00, 0x00, 0x00, 0x00, 0x02, 0x00, 0x40, 0x02, 0x22, 0x22, 0x20, 0x02, 0x22, 0x22, 0x22, 0x00,
0x00, 0x00, 0x00, 0x00, 0x02, 0x00, 0x42, 0x02, 0x02, 0x22, 0x42, 0x00, 0x00, 0x02, 0x02, 0x00,
0x00, 0x00, 0x00, 0x00, 0x02, 0x04, 0x02, 0x02, 0x02, 0x22, 0x42, 0x00, 0x00, 0x02, 0x02, 0x00,
0x00, 0x00, 0x00, 0x00, 0x00, 0x04, 0x02, 0x00, 0x02, 0x22, 0x02, 0x00, 0x00, 0x02, 0x02, 0x00,
0x00, 0x00, 0x00, 0x00, 0x01, 0x04, 0x02, 0x02, 0x02, 0x22, 0x22, 0x02, 0x02, 0x22, 0x02, 0x00,
0x00, 0x00, 0x00, 0x00, 0x00, 0x78, 0x00, 0x01, 0x02, 0x22, 0x00, 0x01, 0x02, 0x41, 0x02, 0x00,
0x00, 0x00, 0x00, 0x00, 0x00, 0x00, 0x00, 0x00, 0x00, 0x00, 0x00, 0x00, 0x00, 0x00, 0x00, 0x00,
0x00, 0x00, 0x00, 0x00, 0x00, 0x00, 0x00, 0x00, 0x00, 0x00, 0x00, 0x00, 0x02, 0x00, 0x00, 0x00,
0x00, 0x00, 0x00, 0x00, 0x00, 0x00, 0x00, 0x00, 0x00, 0x00, 0x00, 0x00, 0x00, 0x00, 0x00, 0x00,
0x00, 0x00, 0x00, 0x00, 0x00, 0x00, 0x00, 0x00, 0x00, 0x00, 0x00, 0x00, 0x00, 0x00, 0x00, 0x00,
0x00, 0x00, 0x00, 0x00, 0x00, 0x00, 0x00, 0x00, 0x00, 0x00, 0x00, 0x00, 0x00, 0x00, 0x00, 0x00,
0x00, 0x00, 0x00, 0x00, 0x00, 0x00, 0x00, 0x00, 0x00, 0x00, 0x00, 0x00, 0x00, 0x00, 0x00, 0x00,
0x00, 0x00, 0x00, 0x00, 0x00, 0x00, 0x00, 0x00, 0x00, 0x00, 0x00, 0x00, 0x00, 0x00, 0x00, 0x00,
0x00, 0x00, 0x00, 0x00, 0x00, 0x00, 0x00, 0x00, 0x00, 0x00, 0x00, 0x00, 0x00, 0x00, 0x00, 0x00,
0x00, 0x00, 0x00, 0x00, 0x00, 0x00, 0x00, 0x00, 0x00, 0x00, 0x00, 0x00, 0x00, 0x00, 0x00, 0x00,
0x00, 0x00, 0x00, 0x00, 0x00, 0x00, 0x00, 0x00, 0x00, 0x00, 0x00, 0x00, 0x00, 0x00, 0x00, 0x00,
0x00, 0x00, 0x00, 0x00, 0x00, 0x00, 0x00, 0x00, 0x00, 0x00, 0x00, 0x00, 0x00, 0x00, 0x00, 0x00,
0x00, 0x00, 0x00, 0x00, 0x00, 0x00, 0x00, 0x00, 0x00, 0x00, 0x00, 0x00, 0x00, 0x00, 0x00, 0x00
};

//Arduino LEDs
const int LED_D9 = 3;
const int LED_D10 = 9;
const int LED_D11 = 5;
const int LED_D12 = 6;
const int LED_D13 = 10;
const int LED_D14 = 11;
const int LED_Transistor = 4;
int LED_D9_Status = 0;
int LED_D10_Status = 0;
int LED_D11_Status = 0;
int LED_D12_Status = 0;
int LED_D13_Status = 0;
int LED_D14_Status = 0;
int led_nachtmodus = 0;

//Arduino Schalter
const int Button_1 = 7;
const int Button_2 = 8;
const int Button_3 = 12;
const int Button_4 = 13;

//Arduino Aktoren
const int Pumpe = 2;
int Pumpe_Auto = 0;
int Pumpe_counter = 0;

//Arduino Sensoren
const int Bodensensor = A3;
const int Wasserstand_1 = A1;
const int Wasserstand_2 = A2;
const int Lichtsensor = A6;
const int Temperatursensor = A7;
int Bodensensor_Messwert = 0;
int Wasserstand_1_Messwert = 0;
int Wasserstand_2_Messwert = 0;
int Lichtsensor_Messwert = 0;
int Temperatursensor_Messwert = 0;
int Temperatur = 0;

//Wichtig statt Delay
unsigned long LED_D10_timeMillis = 0;
unsigned long lastMillis2 = 0;
unsigned long previousMillis1= 0;
unsigned long previousMillis2 = 0;
unsigned long previousMillis3 = 0;
unsigned long previousMillis4 = 0;
const long interval1 = 900000; //15 Minuten
const long interval2 = 900000;
const long interval3 = 900000;
const long interval4 = 3600000;

//Display Menu
int menu = 1;

void setup() {
  //Kommunikation
  Serial.begin(9600);

  //Sensoren und Aktoren
  pinMode(Pumpe, OUTPUT);
  pinMode(Button_1, INPUT);
  pinMode(Button_2, INPUT);
  pinMode(Button_3, INPUT);
  pinMode(Button_4, INPUT);
  pinMode(LED_D9, OUTPUT);
  pinMode(LED_D10, OUTPUT);
  pinMode(LED_D11, OUTPUT);
  pinMode(LED_D12, OUTPUT);
  pinMode(LED_D13, OUTPUT);
  pinMode(LED_D14, OUTPUT);
  pinMode(LED_Transistor, OUTPUT);
  
  //Startsequenz
  //Startsequenz();
  
  //Display Konfigurationen
  display.begin(SSD1306_SWITCHCAPVCC, 0x3C);
  display.display();
  delay(1000);
  display.clearDisplay();
  display.drawBitmap(0, 0, Greenkeeper_IMAGE, 128, 32, WHITE); // display.drawBitmap(x position, y position, bitmap data, bitmap width, bitmap height, color)
  display.display();
  delay(3000);
  
  //Iniziere das Menu
  updateMenu();
  
  //Zeit für blinkende LED
  LED_D10_timeMillis = millis();
  lastMillis2 = millis();
  
  //Dafault für Automatik
  Pumpe_Auto = 1;
  led_nachtmodus = 0;
}
void loop() {
  updateMenu();
}
void Lichtmessung() {
  Lichtsensor_Messwert = analogRead(Lichtsensor);
  Serial.print("Sensorwert = " );
  Serial.println(Lichtsensor_Messwert);
}
void Temperaturmessung() {
  Temperatursensor_Messwert = analogRead(Temperatursensor); 
  Temperatur = map(Temperatursensor_Messwert, 0, 307, 0, 150); 
  Serial.print(Temperatur); 
  Serial.println(" Grad Celsius");
}
void Bewaesserungssystem() {
  //Als erstes wird eine Bodenmessung durchgeführt
  Bodenmessung();
  //Falls der Boden zu trocken ist wird die Pumpe eingeschalten
  if (Bodensensor_Messwert < 50) {
    if (Pumpe_Auto == 1) {
      digitalWrite(Pumpe, HIGH);
      Pumpe_counter ++;
      delay(1000);
      digitalWrite(Pumpe, LOW);
    } else {
      Serial.print("Boden ist Troken Pumpautomatik ist ausgeschalten");
    }  
  } else {
    Serial.print("Boden ist nass genug Sensorwert bei: "+ Bodensensor_Messwert);
  }
}
void Bodenmessung() {
  Bodensensor_Messwert = analogRead(Bodensensor); 
  Serial.print("Feuchtigkeits-Messwert:");
  Serial.println(Bodensensor_Messwert);
  delay(1000);
}
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

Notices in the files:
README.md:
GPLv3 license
